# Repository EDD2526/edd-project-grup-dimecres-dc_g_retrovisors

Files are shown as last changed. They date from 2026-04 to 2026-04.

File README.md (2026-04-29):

View this project on [CADLAB.io](https://cadlab.io/project/30190). 

# Projecte Retrovisors

>**Autors:Carlos Soler Fernandez, Ingrid López Sánchez ** 
>**Versió: final (v.3)**

----------

## Objectiu

>Poder obrir y tancar els retrovisors del cotxe
>Crear els leds de canvi de dirección i angle mort 
>Crear un defoger
>Poder ajustar els retrovisors del cotxe
>Dissenyar i fabricar un sistema electrònic integral per al control de retrovisors
>Gestionar els tres motors amb els finals de carrera on calgui
>Incorporar un sistema que medeixi quan es produeix enlluernament
>Planificar el muntatge de la placa tenint en compte les regles i esoecificacions del fabricant 
>Incorporar un sistema de calefacció i sensors digitals d'angle mort
>Assegurant la viabilitat tècnica i econòmica des del prototip fins a la producció a gran escala

## Diagrama de blocs

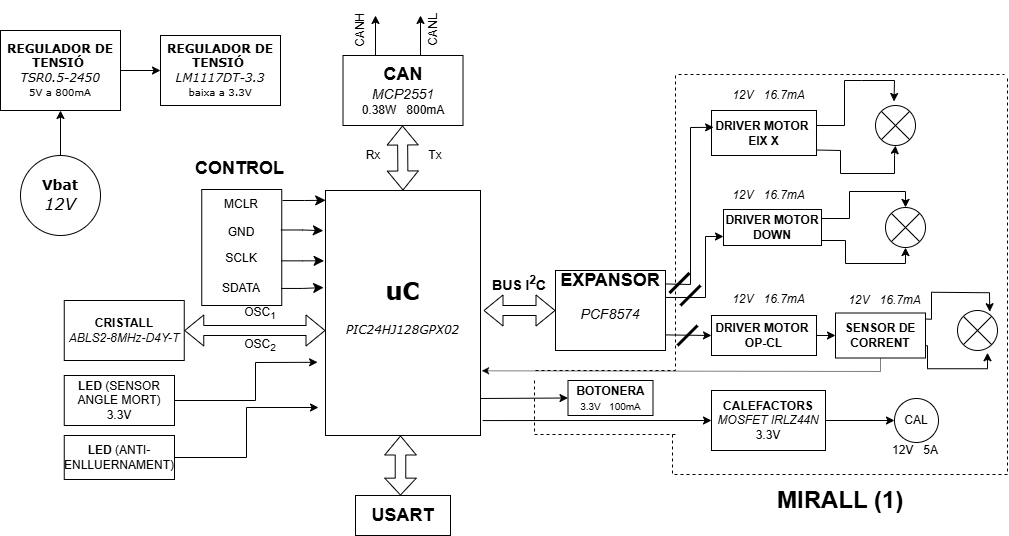
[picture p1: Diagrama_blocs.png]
Diagrama de Blocs


### Descripció/funcionalitat de cada bloc

  *

-----------

## Requisits / Especificacions

  * Alimentació; 12V, regulada 5V
  * Microcontrolador PIC18xxxxxxxxx
  * ...

-----------

## Components

| Descripci&#243; | Ref | Package |Datasheet | Prove&#239;dor | Preu | Unitats |
| --- | --- | --- | --- | ---| --- | --- |
| Microcontrolador | PIC18F26Q83-I/SS | SOIC-28 |[Datasheet](https://www.mouser.es/datasheet/2/268/PIC18F27_47_57Q83_Preliminary_Data_Sheet_40002265B-2887591.pdf) | [Mouser](https://www.mouser.es/c/?q=PIC18F27Q83-I%2FSO)| 2,17&euro;| 1x |
| XTAL-Ressonador | CSTCR7M99G53-R0 | SMD |[Datasheet](https://www.mouser.es/datasheet/2/281/p16e-522700.pdf) | [Mouser](https://www.mouser.es/ProductDetail/Murata-Electronics/CSTCR7M99G53-R0?qs=Zd9RUO93%2Fo7cnwzsujIkpA%3D%3D)  | 0,27&euro; | 1x |

-----------

## Software

### Eines:

  * KiCad 9.0 o superior
  * 

### Configuraci&#243; :

  * 

### Funcionalitats:

  * 

-----------

## Historial de canvis

| Data | Autor | Branch | Versi&#243; | Descripci&#243; |
| --- | --- | --- | --- | --- |
| 11/03/2026 | iingridlopez | Master | prova | Inici del projecte 
| 17/03/2026 | canals-ub | Master | Backlink added | Backlink to CADLAB.io has been added. 
| 17/03/2026 | Carlosolerfernandez | Master | Create project kicad | Inici del projecte en KiCad 
| 17/03/2026 | Carlosolerfernandez | Master | Inici kiCat | Primera versió de l'esquemàtic 
| 17/03/2026 | Carlosolerfernandez | Master | Inici proyecta kicat | Configuració de fitxers inicials 
| 17/03/2026 | Carlosolerfernandez | Master | Etapa de alimentació 1 | Disseny de la primera part d'alimentació 
| 17/03/2026 | Carlosolerfernandez | Master | Etapa de alimentacio completa | Finalització de l'etapa d'alimentació 
| 17/03/2026 | Carlosolerfernandez | Master | Alimentacio finalitzada e inici de micro | Transició al disseny del microcontrolador 
| 18/03/2026 | Carlosolerfernandez | Master | microcontrolador i driver | Afegit microcontrolador i perifèrics 
| 22/03/2026 | Carlosolerfernandez | Master | Correcio gnd, proposicio canvi de micro | Correcció de masses i revisió de components 
| 23/03/2026 | Carlosolerfernandez | Master | Reorganització proyecte, inici conexions CAN | Gestió del bus CAN 
| 23/03/2026 | Carlosolerfernandez | Master | Part Micro quasi completat | Falta afegir etiquetes de potencia 
| 24/03/2026 | Carlosolerfernandez | Master | Microprocessador finalissim | Placement de alimentacion y micro 
| 25/03/2026 | Carlosolerfernandez | Master | Diagrama de Blocs Afegit | Canvi del swicht1 to push botton5 
| 29/03/2026 | iingridlopez | Branca Nova | Creacio de branca nova i update | Inici de nova branca de treball 
| 07/04/2026 | iingridlopez | Master | actualització (NO VERSIÓ FINAL) | Sincronització de canvis |
| 08/04/2026 | iingridlopez | Master | esquematic + placement | Falta routing dels drivers 
| 08/04/2026 | Carlosolerfernandez | Master | README | Creació del fitxer de documentació 
| 08/04/2026 | iingridlopez | Master | añadido el readme | Actualització de documentació 
| 08/04/2026 | Carlosolerfernandez | Master | Modificació placement | Ajustos en la placa 
| 08/04/2026 | iingridlopez | Master | prueba para unir a la main | Test de merge 
| 08/04/2026 | iingridlopez | Master | Merge con resolución de conflictos | Unió de branques en KiCad 
| 08/04/2026 | Carlosolerfernandez | Master | afegim diagrama | Actualització gràfica del projecte 
| 08/04/2026 | Carlosolerfernandez | Master | Correccion Readme | Revisió de textos 
| 08/04/2026 | Carlosolerfernandez | Master | eliminamos GND PWR | Modificació de tots els GND 
| 10/04/2026 | iingridlopez | Master | millora de placement | Optimització d'espai 
| 13/04/2026 | Carlosolerfernandez | Master | Enrotament Part digital finalitzada | Finalització del routing digital |

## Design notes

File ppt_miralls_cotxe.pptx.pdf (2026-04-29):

# MÒDUL D’AUTOMÒBIL: RETROVISORS

# Posar en pràctica els coneixements adquirits durant el curs per a desenvolupar un sistema electrònic seguint el flux de disseny de PCBs amb temàtica de projectes

d’automoció.

## Grau d’Enginyeria Electrònica de Telecomunicacions: Facultat de Física- UB

## Eines de Disseny - 2026

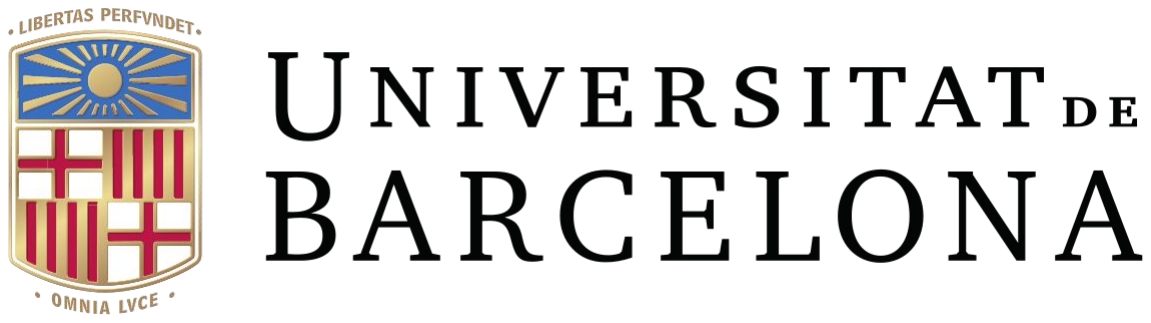
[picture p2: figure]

## Carlos Soler Fernandez, Ingrid Lopez Sanchez

Objectius | Components | Diagrama de blocs | Esquemàtic | Simulació | Layout | Pressupost

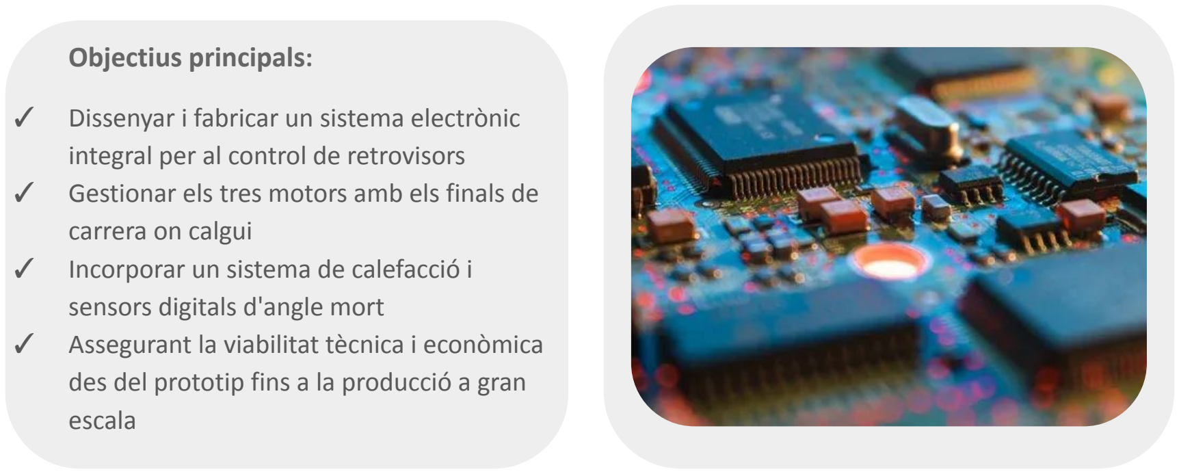
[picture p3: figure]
Objectius principals:; integral per al control de retrovisors; carrera on calgui ✓ Incorporar un sistema de calefacció i; sensors digitals d'angle mort; escala

## ✓ Dissenyar i fabricar un sistema electrònic

## ✓ Gestionar els tres motors amb els finals de

## ✓ Assegurant la viabilitat tècnica i econòmica des del prototip fins a la producció a gran

1

## DATASHEETS

## PIC24HJ128GPX02 (https://ww1.microchip.com/downloads/en/DeviceDoc/70293G.pdf)

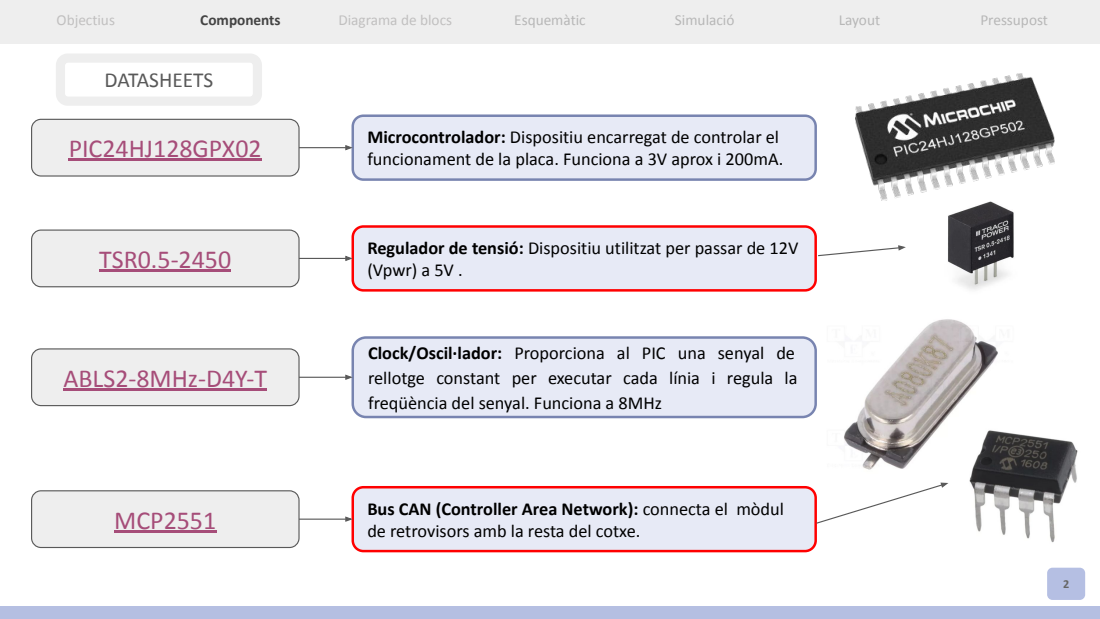
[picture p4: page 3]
TSR0.5-2450; ABLS2-8MHz-D4Y-T; MCP2551

Microcontrolador: Dispositiu encarregat de controlar el
funcionament de la placa. Funciona a 3V aprox i 200mA.

Regulador de tensió: Dispositiu utilitzat per passar de 12V
(Vpwr) a 5V .

Clock/Oscil·lador: Proporciona al PIC una senyal de
rellotge constant per executar cada línia i regula la
freqüència del senyal. Funciona a 8MHz

Bus CAN (Controller Area Network): connecta el mòdul
de retrovisors amb la resta del cotxe.

## DATASHEETS

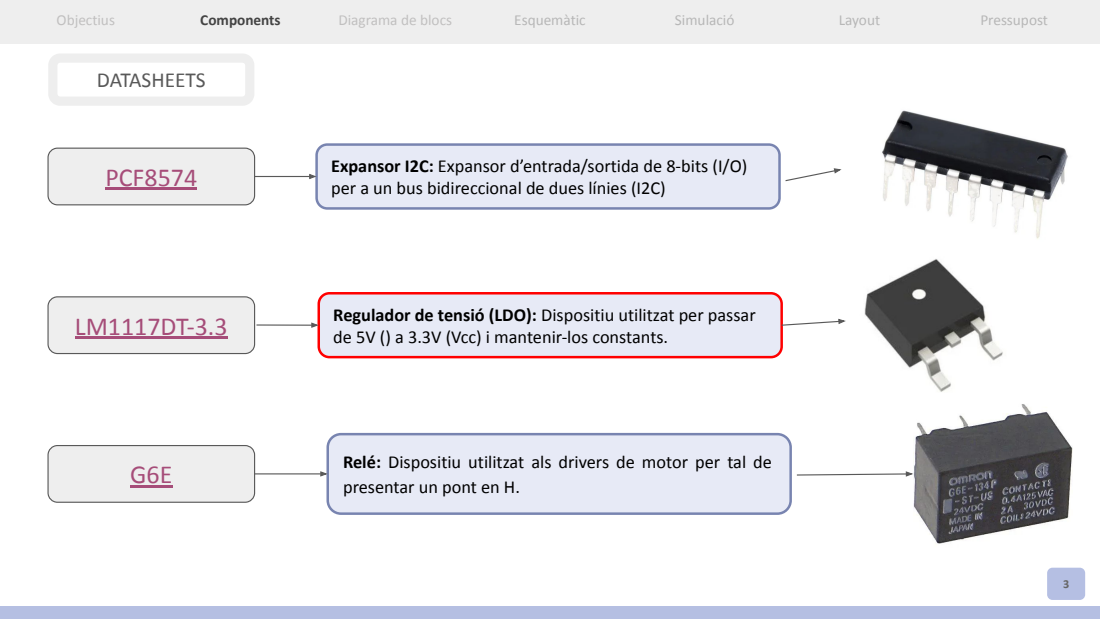
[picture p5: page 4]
PCF8574

Expansor I2C: Expansor d’entrada/sortida de 8-bits (I/O)
per a un bus bidireccional de dues línies (I2C)

Regulador de tensió (LDO): Dispositiu utilitzat per passar
de 5V () a 3.3V (Vcc) i mantenir-los constants.

Relé: Dispositiu utilitzat als drivers de motor per tal de
presentar un pont en H.

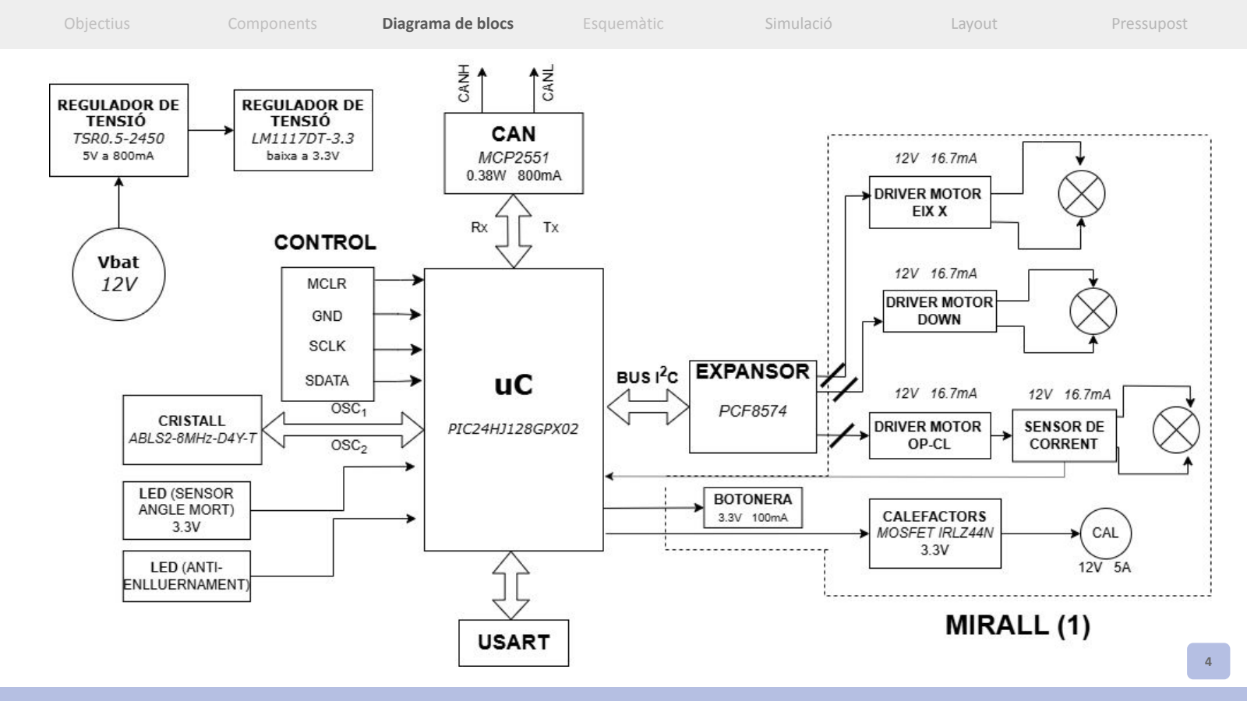
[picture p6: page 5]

4

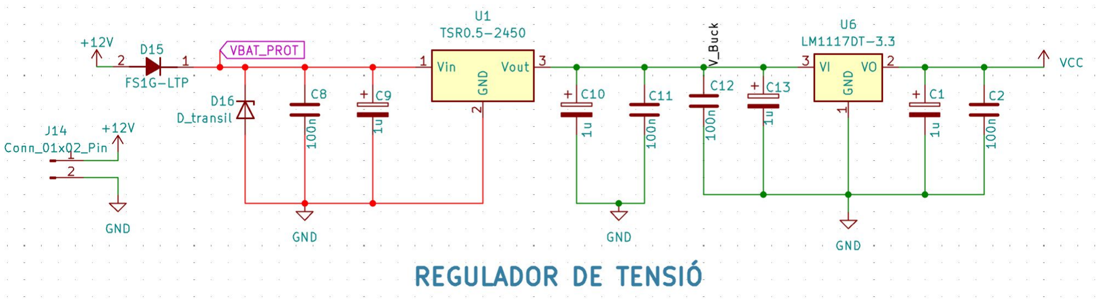
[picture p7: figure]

5

## REGULADOR DE TENSIÓ

## LED’S

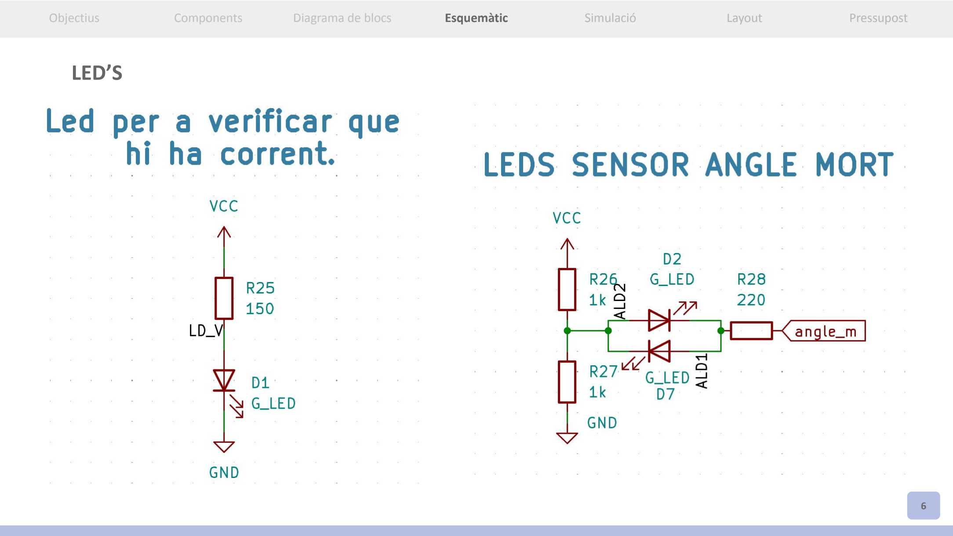
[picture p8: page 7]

6

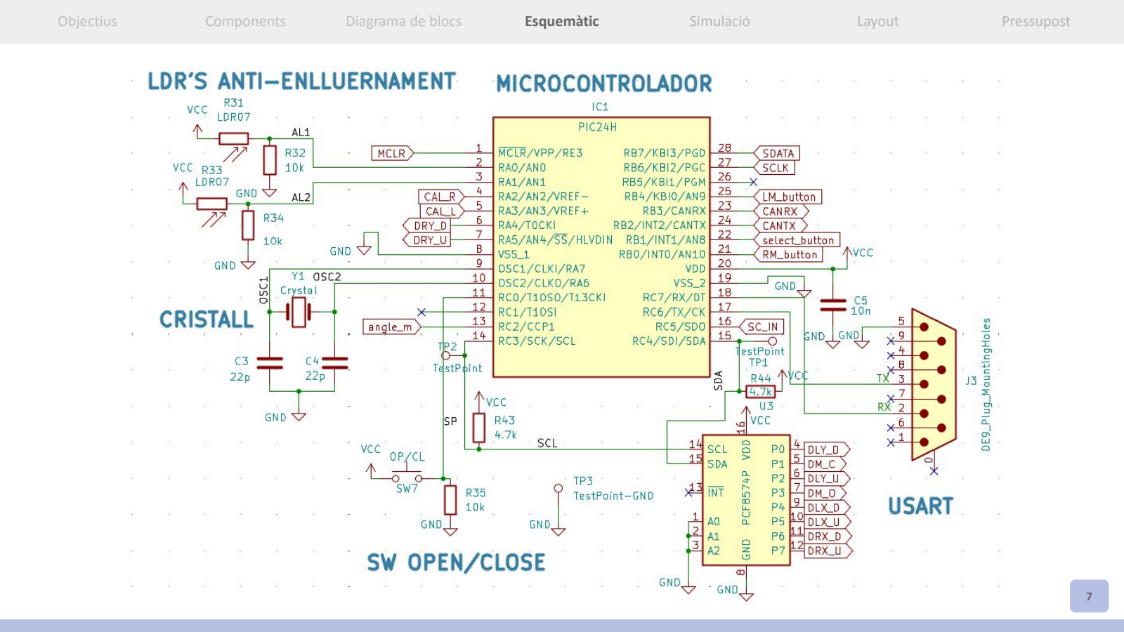
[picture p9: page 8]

7

8

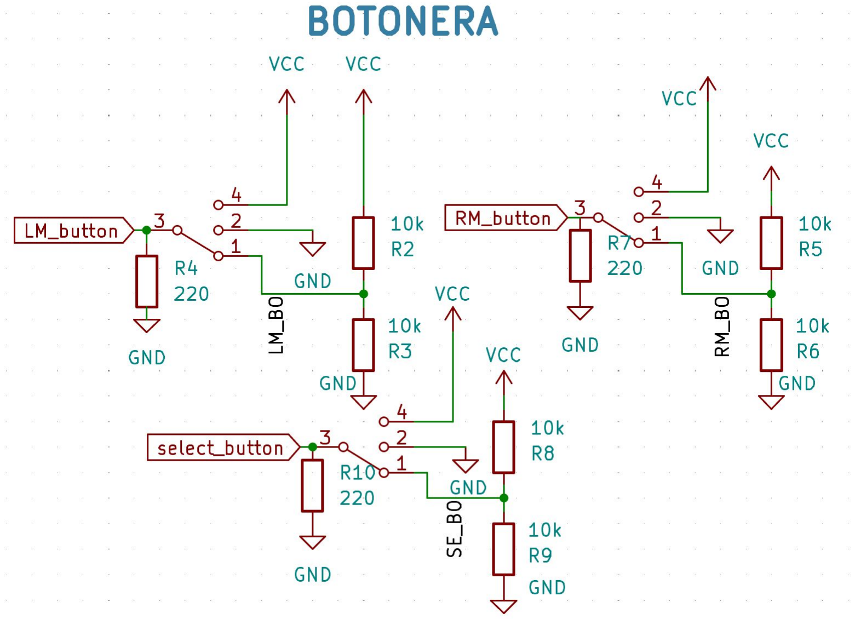
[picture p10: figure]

## FASE DIGITAL

## FASE DIGITAL

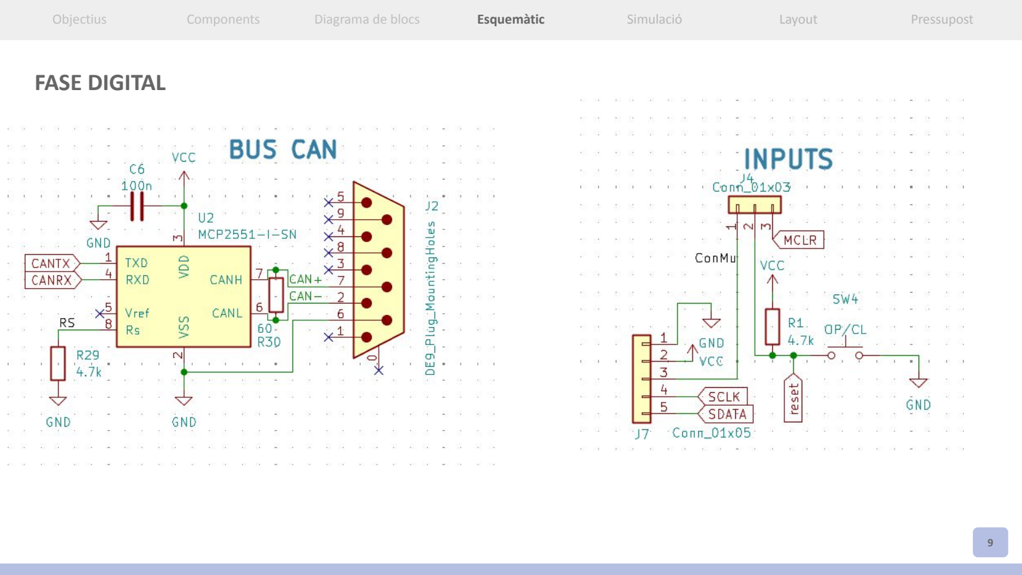
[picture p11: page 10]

9

## FASE DE POTÈNCIA

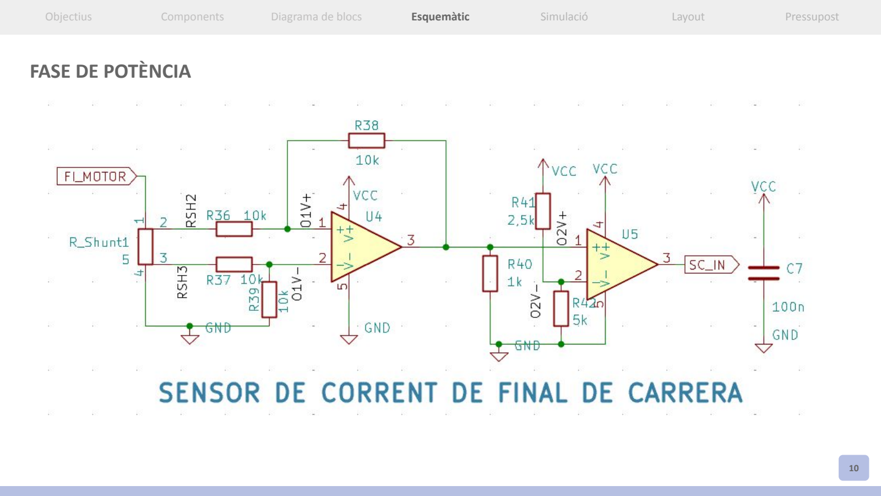
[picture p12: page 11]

10

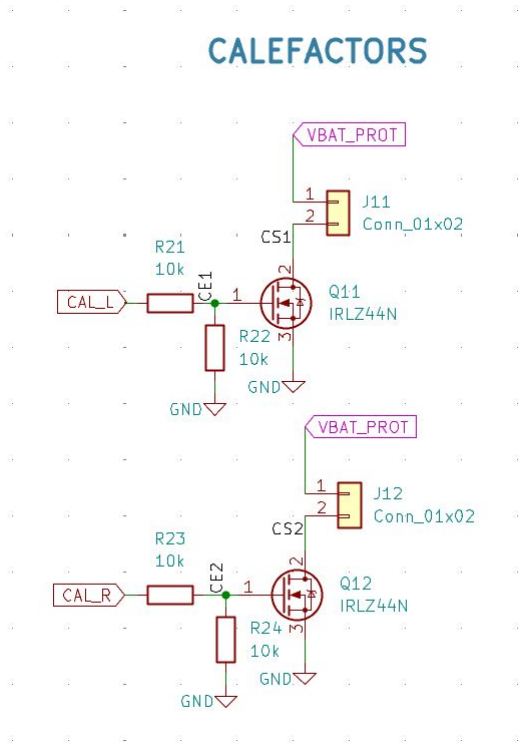
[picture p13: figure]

11

## FASE DE POTÈNCIA

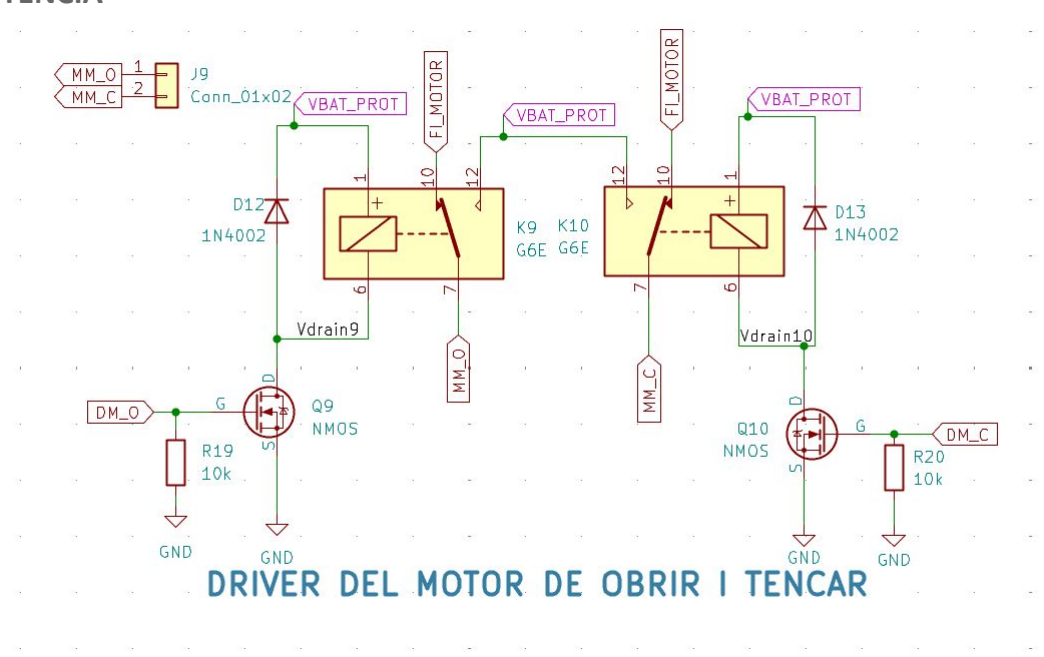
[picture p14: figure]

12

## FASE DE POTÈNCIA

## FASE DE POTÈNCIA

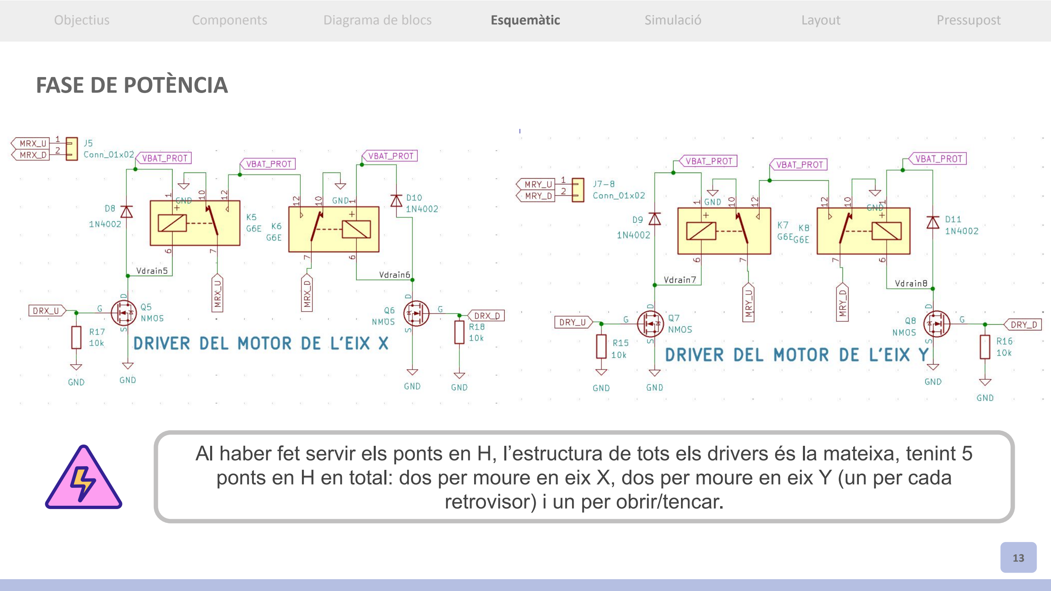
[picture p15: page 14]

13

Al haber fet servir els ponts en H, l’estructura de tots els drivers és la mateixa, tenint 5

## ponts en H en total: dos per moure en eix X, dos per moure en eix Y (un per cada

retrovisor) i un per obrir/tencar.

SIMULACIÓ: SENSOR DE CORRENT;

## FINAL DE CARRERA OP/CL

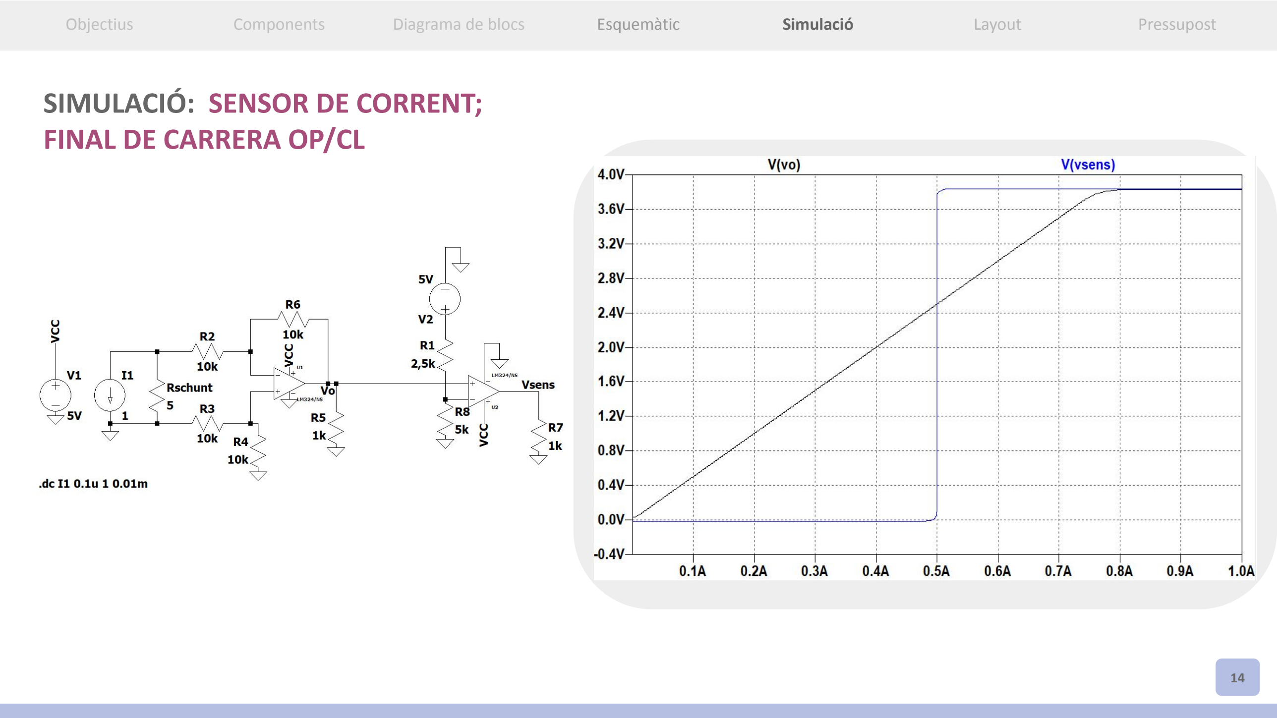
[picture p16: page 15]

14

## SIMULACIÓ: RELÉS

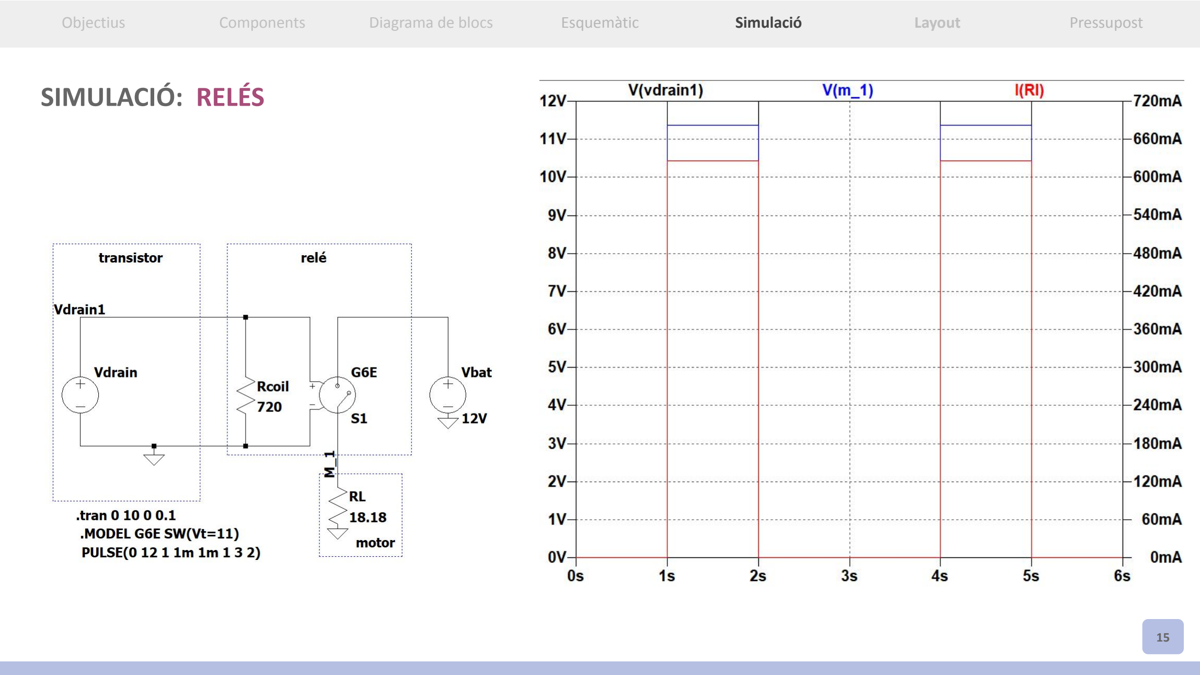
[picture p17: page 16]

15

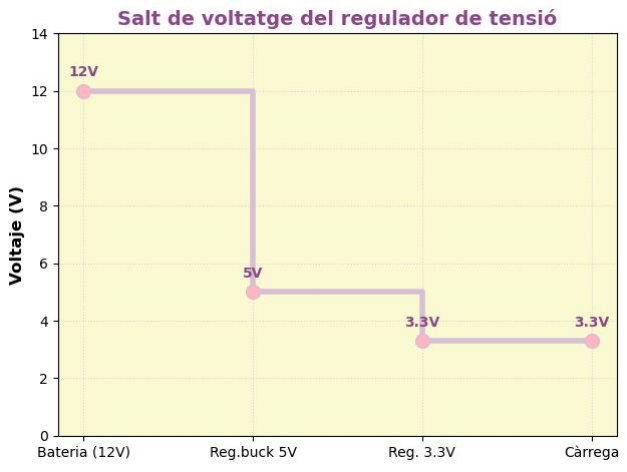
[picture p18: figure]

16

## SIMULACIÓ: PART ALIMENTACIÓ, BUCK I REGULADOR DE TENSIÓ

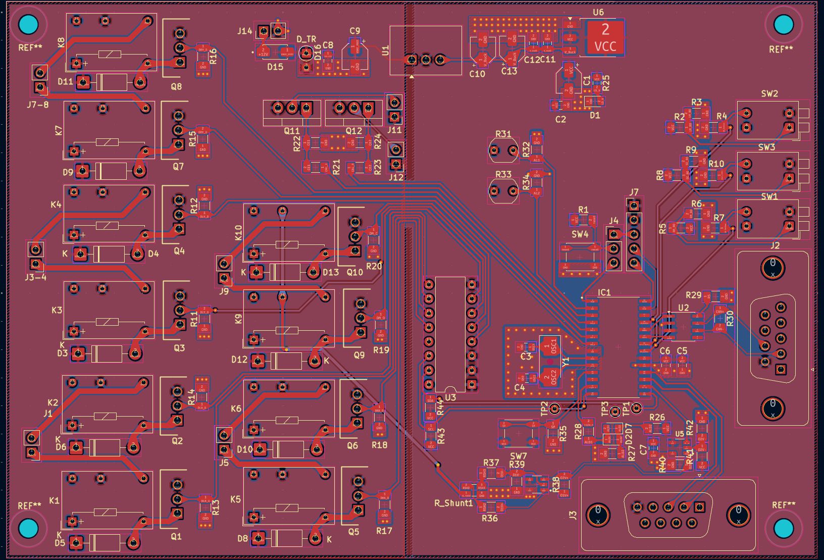
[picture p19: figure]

17

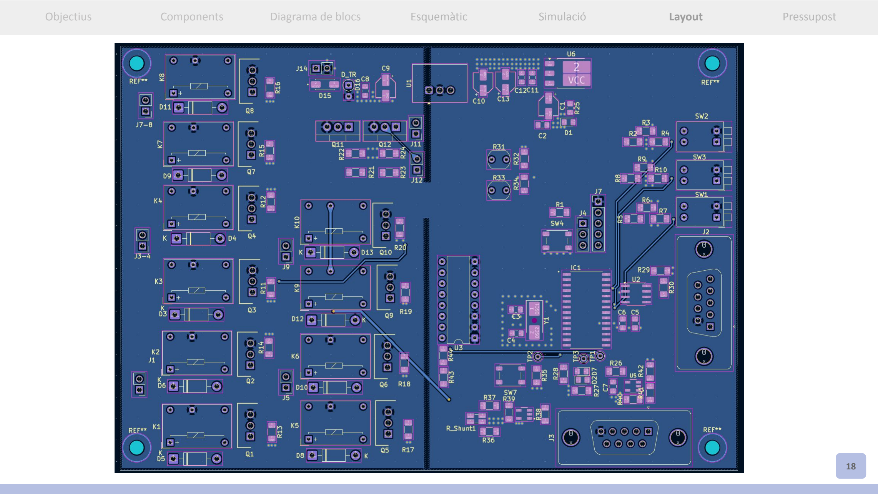
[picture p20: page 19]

18

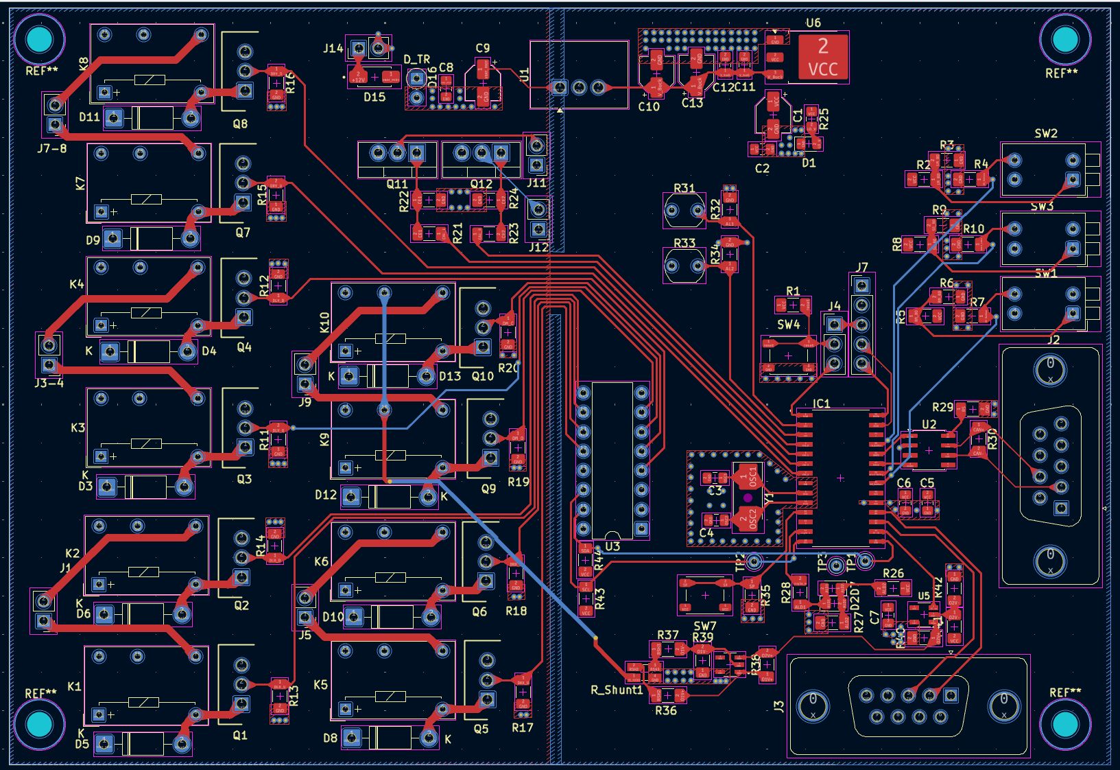
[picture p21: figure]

19

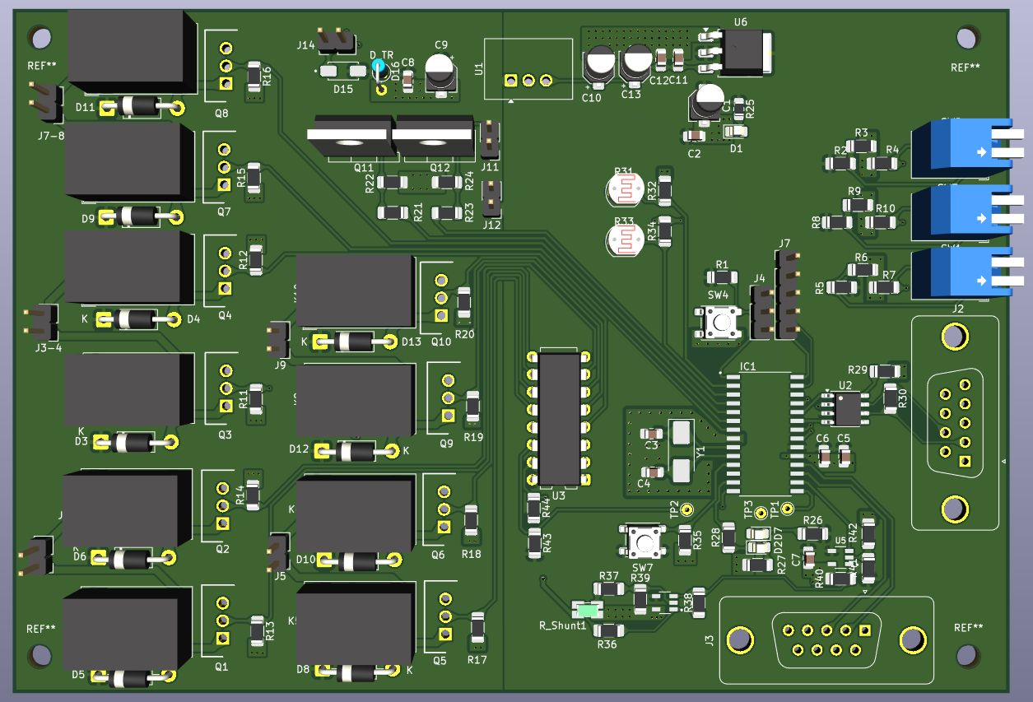
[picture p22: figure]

20

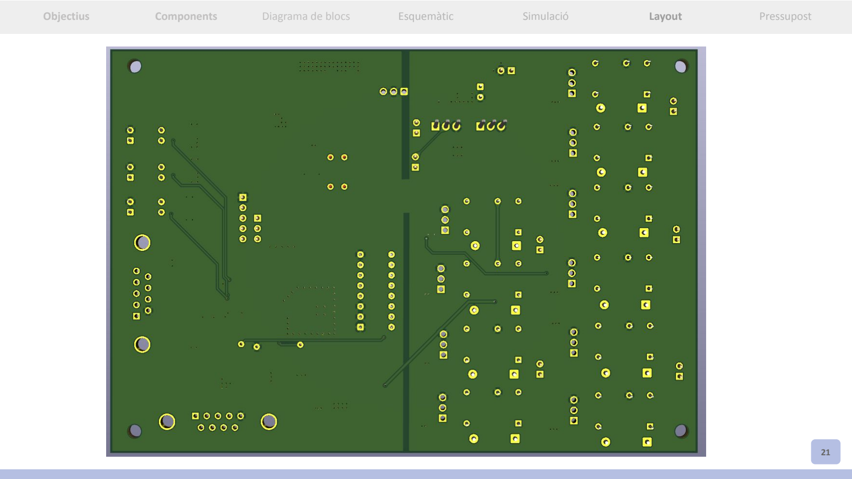
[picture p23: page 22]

21

22

| x1 PLACA | x10 PLAQUES | x50 PLAQUES | x1000 PLAQUES | x20000 PLAQUES
PREU TOTAL COMPONENTS (€) | 67,47 | 625,04 | 2876,27 | 42681,19 | 842069,8

23

| x1 PLACA | x10 PLAQUES | x50 PLAQUES | x1000 PLAQUES | x20000 PLAQUES
PREU TOTAL COMPONENTS (€) | 67,47 | 625,04 | 2876,27 | 42681,19 | 842069,8
PREU ELABORACIÓ PLACA (€) | 11,50 | 14,50 | 37 | 390,41 | 7028,52
PREU PER PLACA (€) | 78,97 | 63,95 | 58,27 | 44,07 | 42,45
PREU TOTAL (€) | 78,97 | 639,54 | 2913,27 | 44071,6 | 849098,32

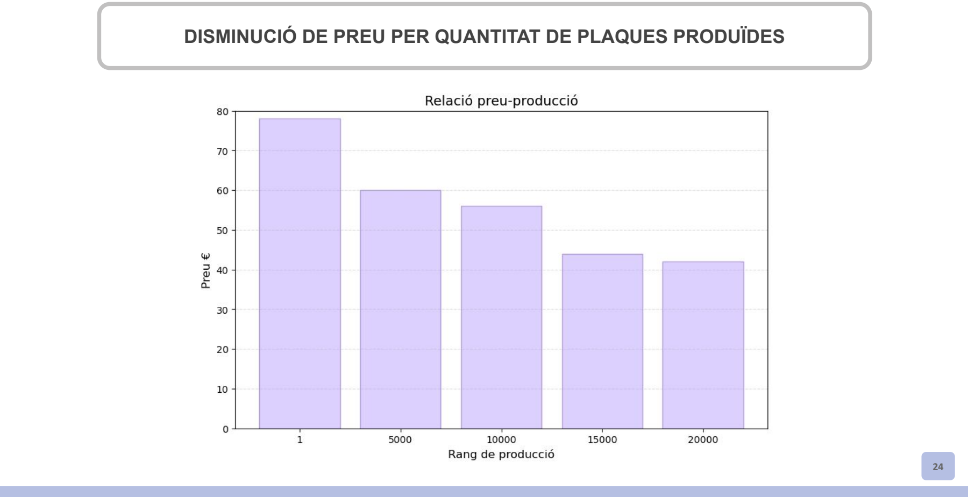
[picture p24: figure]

## DISMINUCIÓ DE PREU PER QUANTITAT DE PLAQUES PRODUÏDES

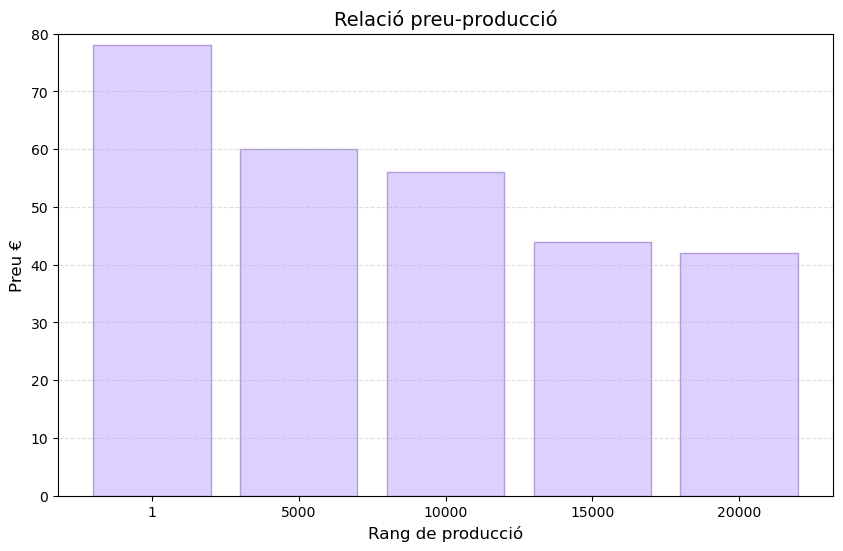
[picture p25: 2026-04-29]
graf_preu_prod.png

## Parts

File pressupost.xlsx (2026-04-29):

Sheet: Retrovisors_Carlos_Soler_Ingrid
# | Reference | Qty | Value | Footprint | DNP | P x1 (€) | P x10 (€) | P x50 (€) | P x1000 (€) | P x20000 (€)
1 | C1, C9, C10, C13 | 4 | 1u | Capacitor_SMD:CP_Elec_4x5.7
2 | C2, C6, C7, C8, C11, C12 | 6 | 100n | Capacitor_SMD:C_0805_2012Metric_Pad1.18x1.45mm_HandSolder
3 | C3, C4 | 2 | 22p | Capacitor_SMD:C_0805_2012Metric_Pad1.18x1.45mm_HandSolder
4 | C5 | 1 | 10n | Capacitor_SMD:C_0805_2012Metric_Pad1.18x1.45mm_HandSolder
5 | D1, D2, D7 | 3 | G_LED | LED_SMD:LED_0805_2012Metric_Pad1.15x1.40mm_HandSolder |  | 0.38 | 2.46 | 12.3 | 94.73 | 1994.6
6 | D3, D4, D5, D6, D8, D9, D10, D11, D12, D13 | 10 | 1N4002 | Diode_THT:D_DO-41_SOD81_P10.16mm_Horizontal
7 | D15 | 1 | FS1G-LTP | AA_footprints:DIOM5225X244N
8 | D16 | 1 | D_transil | Diode_THT:D_DO-35_SOD27_P2.54mm_Vertical_AnodeUp
9 | IC1 | 1 | PIC24H | AA_footprints:SOIC127P1030X265-28N
10 | J1, J3-4, J5, J7-8, J9, J11, J12 | 7 | Conn_01x02 | Connector_PinHeader_2.54mm:PinHeader_1x02_P2.54mm_Vertical
11 | J2, J3 | 2 | DE9_Plug_MountingHoles | AA_footprints:DSUB-9_Female_Vertical_Pitch2.77x2.84mm_MountingHoles
12 | J4 | 1 | Conn_01x03 | Connector_PinHeader_2.54mm:PinHeader_1x03_P2.54mm_Vertical
13 | J7 | 1 | Conn_01x05 | Connector_PinHeader_2.54mm:PinHeader_1x05_P2.54mm_Vertical
14 | J14 | 1 | Conn_01x02_Pin | Connector_PinHeader_2.54mm:PinHeader_1x02_P2.54mm_Vertical
15 | K1, K2, K3, K4, K5, K6, K7, K8, K9, K10 | 10 | G6E | Relay_THT:Relay_SPDT_Omron_G6E
16 | Q1, Q2, Q3, Q4, Q5, Q6, Q7, Q8, Q9, Q10 | 10 | NMOS | AA_footprints:TO254P470X1016X1965-3P
17 | Q11, Q12 | 2 | IRLZ44N | Package_TO_SOT_THT:TO-220-3_Vertical
18 | R1, R29, R43, R44 | 4 | 4.7k | Resistor_SMD:R_1206_3216Metric_Pad1.30x1.75mm_HandSolder
19 | R2, R3, R5, R6, R8, R9, R11, R12, R13, R14, R15, R16, R17, R18, R19, R20, R21, R22, R23, R24, R32, R34, R35, R36, R37, R38, R39 | 27 | 10k | Resistor_SMD:R_1206_3216Metric_Pad1.30x1.75mm_HandSolder
20 | R4, R7, R10, R28 | 4 | 220 | Resistor_SMD:R_1206_3216Metric_Pad1.30x1.75mm_HandSolder
21 | R25 | 1 | 150 | Resistor_SMD:R_0805_2012Metric_Pad1.20x1.40mm_HandSolder
22 | R26, R27, R40 | 3 | 1k | Resistor_SMD:R_1206_3216Metric_Pad1.30x1.75mm_HandSolder
23 | R30 | 1 | 60 | Resistor_SMD:R_1206_3216Metric_Pad1.30x1.75mm_HandSolder
24 | R31, R33 | 2 | LDR07 | OptoDevice:R_LDR_5.1x4.3mm_P3.4mm_Vertical
25 | R41 | 1 | 2,5k | Resistor_SMD:R_1206_3216Metric_Pad1.30x1.75mm_HandSolder
26 | R42 | 1 | 5k | Resistor_SMD:R_1206_3216Metric_Pad1.30x1.75mm_HandSolder
27 | R_Shunt1 | 1 | 5 | Resistor_SMD:R_Shunt_Ohmite_LVK12
28 | SW1, SW2, SW3 | 3 | SW_DP3T | Button_Switch_THT:SW_DIP_SPSTx02_Piano_10.8x6.64mm_W7.62mm_P2.54mm
29 | SW4, SW7 | 2 | OP/CL | Button_Switch_SMD:SW_SPST_PTS647_Sx38
30 | TP1, TP2 | 2 | TestPoint | TestPoint:TestPoint_THTPad_D1.5mm_Drill0.7mm
31 | TP3 | 1 | TestPoint-GND | TestPoint:TestPoint_THTPad_D1.5mm_Drill0.7mm
32 | U1 | 1 | TSR0.5-2450 | Converter_DCDC:Converter_DCDC_TRACO_TSR0.5-24xx_TSR0.5-24xxx_THT
33 | U2 | 1 | MCP2551-I-SN | Package_SO:SOIC-8_3.9x4.9mm_P1.27mm
34 | U3 | 1 | PCF8574P | Package_DIP:DIP-16_W7.62mm
35 | U4, U5 | 2 | type="X" model="OPAMP" lib="" | AA_footprints:SOT95P280X145-5N
36 | U6 | 1 | LM1117DT-3.3 | Package_TO_SOT_SMD:TO-252-3_TabPin2
37 | Y1 | 1 | Crystal | Crystal:Crystal_SMD_Abracon_ABM3-2Pin_5.0x3.2mm_HandSoldering

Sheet: total_components
Concepto | x1 PLACA | x10 PLAQUES | x50 PLAQUES | x1000 PLAQUES | x20000 PLAQUES
PREU TOTAL COMPONENTS (€) | 67.47 | 625.04 | 2876.27 | 42681.19 | 842069.8

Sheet: total_placa
Concepto | x1 PLACA | x10 PLAQUES | x50 PLAQUES | x1000 PLAQUES | x20000 PLAQUES
PREU TOTAL COMPONENTS (€) | 67.47 | 625.04 | 2876.27 | 42681.19 | 842069.8 | TOTAL | 1 | 10 | 50 | 1000 | 20000
PREU ELABORACIÓ PLACA (€) | 11.5 | 14.5 | 37 | 390.41 | 7028.52 | PREU TOTAL (€) | 78.97 | 639.54 | 2913.27 | 44071.6 | 849098.32
PREU PER PLACA (€) | 78.97 | 63.95 | 58.27 | 44.07 | 42.45
PREU TOTAL (€) | 78.97 | 639.54 | 2913.27 | 44071.6 | 849098.32

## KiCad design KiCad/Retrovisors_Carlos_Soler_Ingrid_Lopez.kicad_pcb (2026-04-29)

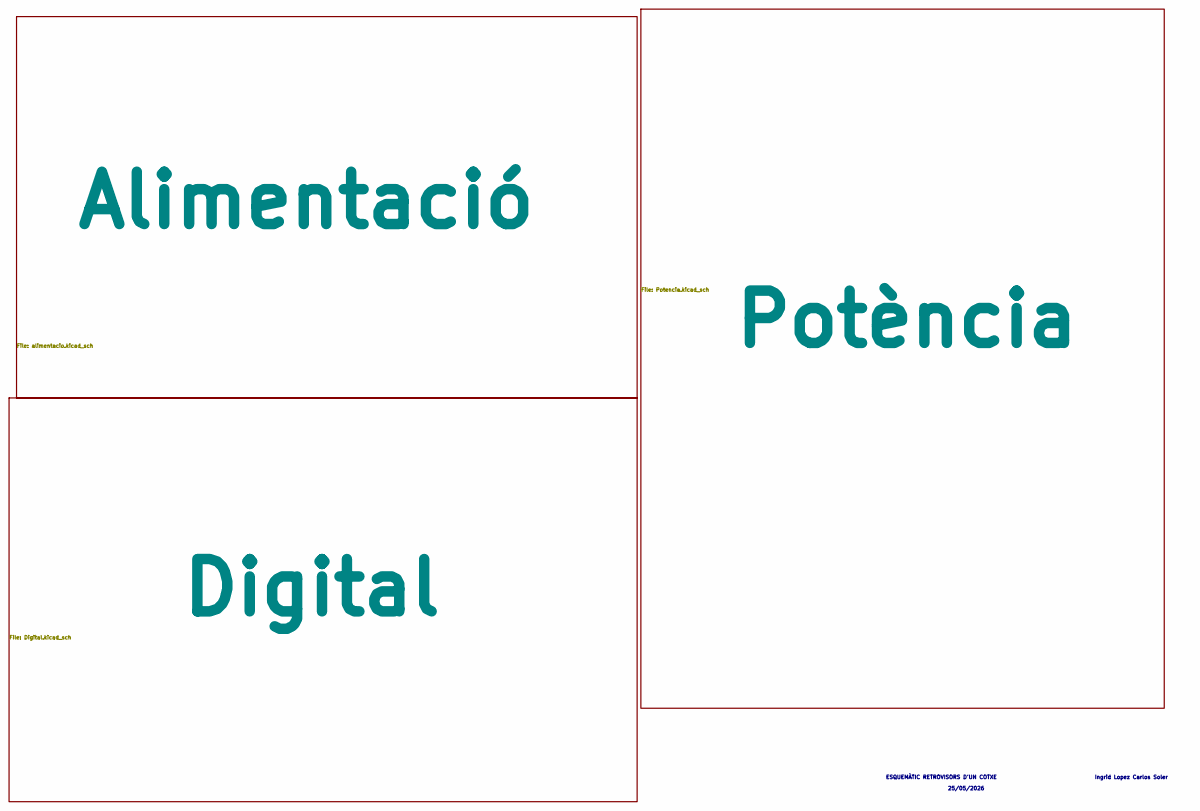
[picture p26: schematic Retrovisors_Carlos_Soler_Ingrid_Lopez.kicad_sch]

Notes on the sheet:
Ingrid Lopez Carlos Soler
ESQUEMÀTIC RETROVISORS D'UN COTXE
25/05/2026

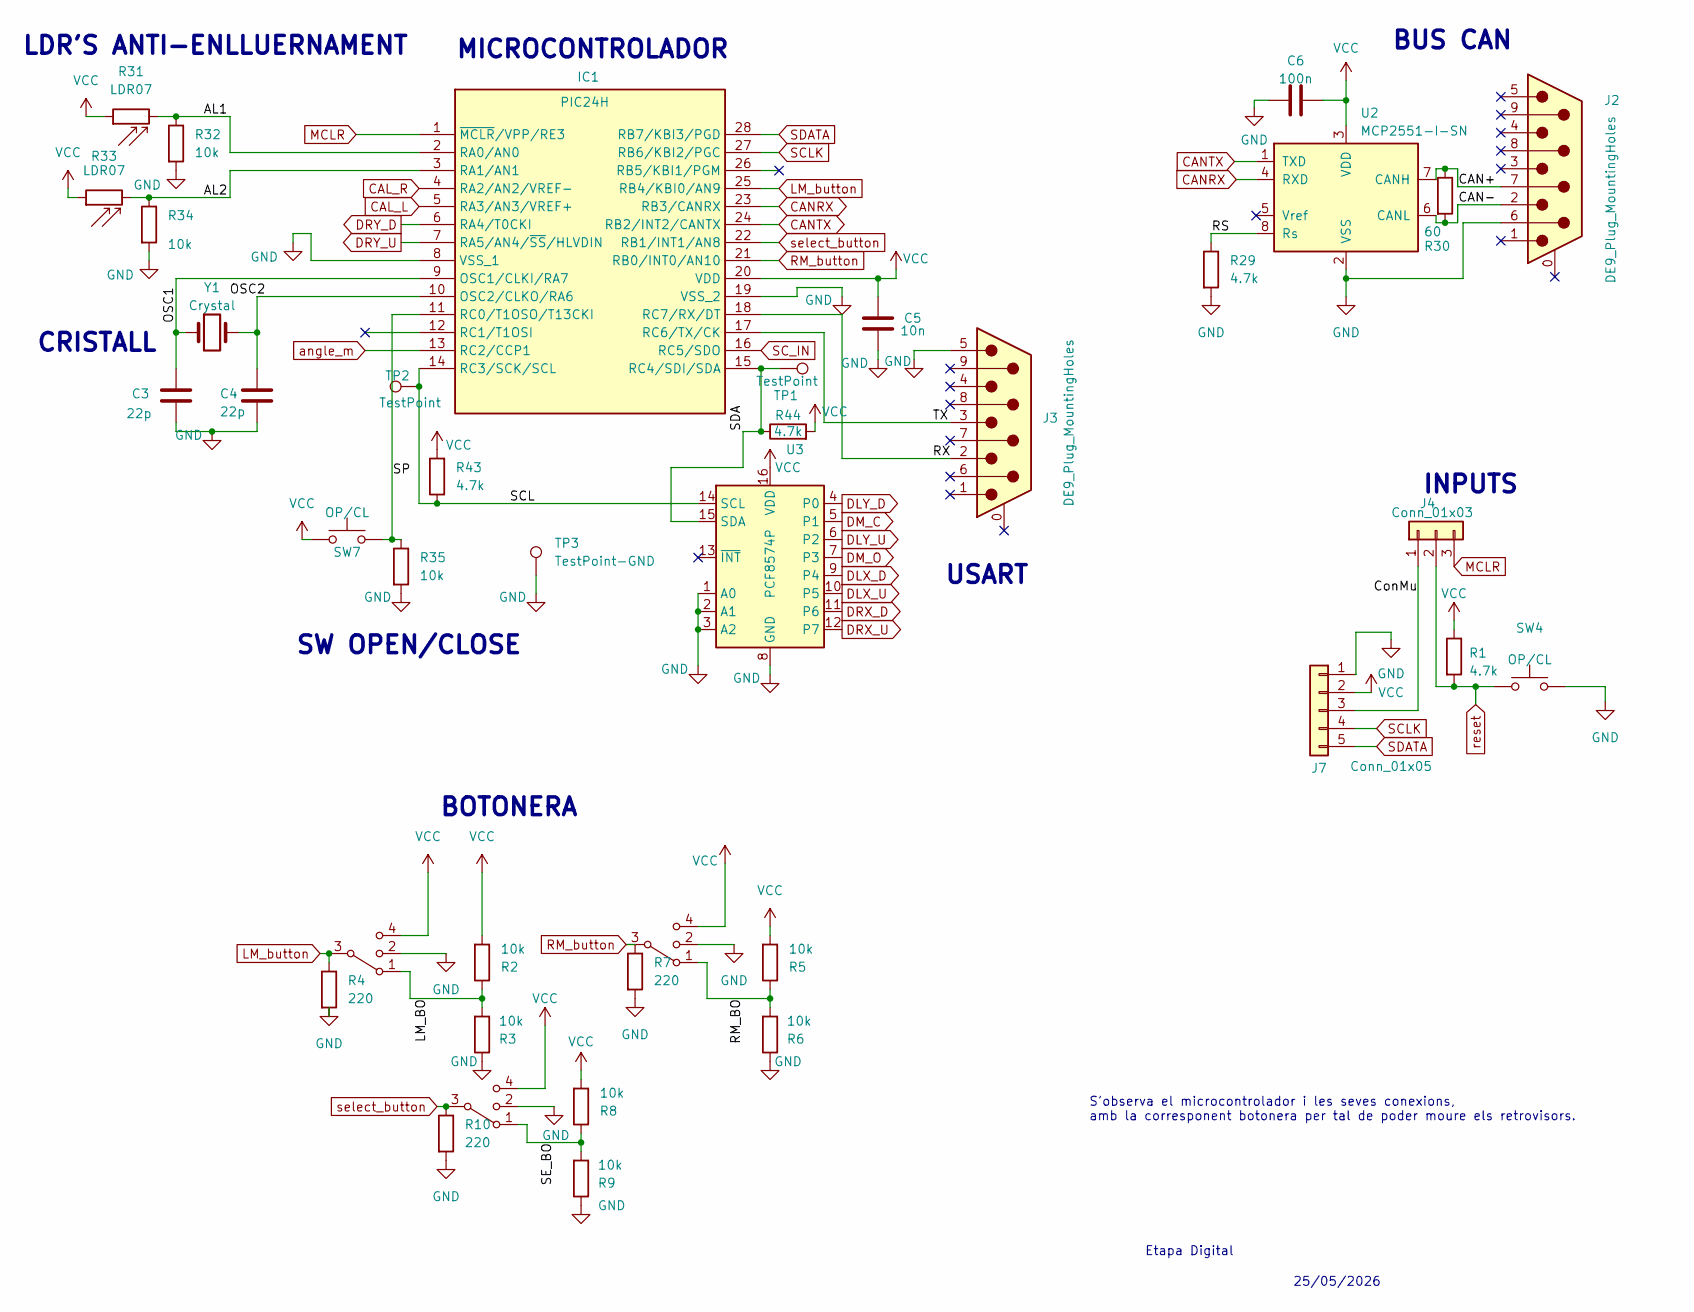
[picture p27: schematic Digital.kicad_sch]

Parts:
C3, C4: 22p; C_0805_2012Metric_Pad1.18x1.45mm_HandSolder
C5: 10n; C_0805_2012Metric_Pad1.18x1.45mm_HandSolder
C6: 100n; C_0805_2012Metric_Pad1.18x1.45mm_HandSolder
IC1: PIC24H; SOIC127P1030X265-28N; Manufacturer_Part_Number PIC18F2580-I/SO; Mouser Part Number 579-PIC18F2580-I/SO
J2, J3: DE9_Plug_MountingHoles; DSUB-9_Female_Vertical_Pitch2.77x2.84mm_MountingHoles
J4: Conn_01x03; PinHeader_1x03_P2.54mm_Vertical
J7: Conn_01x05; PinHeader_1x05_P2.54mm_Vertical
R1, R29, R43, R44: 4.7k; R_1206_3216Metric_Pad1.30x1.75mm_HandSolder
R2, R3, R5, R6, R8, R9, R32, R34, R35: 10k; R_1206_3216Metric_Pad1.30x1.75mm_HandSolder
R4, R7, R10: 220; R_1206_3216Metric_Pad1.30x1.75mm_HandSolder
R30: 60; R_1206_3216Metric_Pad1.30x1.75mm_HandSolder
R31, R33: LDR07; R_LDR_5.1x4.3mm_P3.4mm_Vertical
SW1, SW2, SW3: SW_DP3T; SW_DIP_SPSTx02_Piano_10.8x6.64mm_W7.62mm_P2.54mm
SW4, SW7: OP/CL; SW_SPST_PTS647_Sx38
TP1, TP2: TestPoint; TestPoint_THTPad_D1.5mm_Drill0.7mm
TP3: TestPoint-GND; TestPoint_THTPad_D1.5mm_Drill0.7mm
U2: MCP2551-I-SN; SOIC-8_3.9x4.9mm_P1.27mm
U3: PCF8574P; DIP-16_W7.62mm
Y1: Crystal; Crystal_SMD_Abracon_ABM3-2Pin_5.0x3.2mm_HandSoldering

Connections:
/Digital/AL1: IC1.2 (RA0/AN0), R31.2, R32.1
/Digital/AL2: IC1.3 (RA1/AN1), R33.2, R34.1
/Digital/CAN+: J2.7, R30.1, U2.7 (CANH)
/Digital/CAN-: J2.2, R30.2, U2.6 (CANL)
/Digital/ConMu: J4.1, J7.3
/Digital/LM_BO: R2.1, R3.2, SW2.1
/Digital/OSC1: C3.1, IC1.9 (OSC1/CLKI/RA7), Y1.1
/Digital/OSC2: C4.1, IC1.10 (OSC2/CLKO/RA6), Y1.2
/Digital/RM_BO: R5.1, R6.2, SW1.1
/Digital/RS: R29.1, U2.8 (Rs)
/Digital/RX: IC1.18 (RC7/RX/DT), J3.2
/Digital/SCL: IC1.14 (RC3/SCK/SCL), R43.1, TP2.1, U3.14 (SCL)
/Digital/SDA: IC1.15 (RC4/SDI/SDA), R44.1, TP1.1, U3.15 (SDA)
/Digital/SE_BO: R8.1, R9.2, SW3.1
/Digital/SP: IC1.11 (RC0/T1OSO/T13CKI), R35.1, SW7.2
/Digital/TX: IC1.17 (RC6/TX/CK), J3.3
CAL_L: IC1.5 (RA3/AN3/VREF+); also elsewhere on the board
CAL_R: IC1.4 (RA2/AN2/VREF-); also elsewhere on the board
CANRX: IC1.23 (RB3/CANRX), U2.4 (RXD)
CANTX: IC1.24 (RB2/INT2/CANTX), U2.1 (TXD)
DLX_D: U3.9 (P4); also elsewhere on the board
DLX_U: U3.10 (P5); also elsewhere on the board
DLY_D: U3.4 (P0); also elsewhere on the board
DLY_U: U3.6 (P2); also elsewhere on the board
DM_C: U3.5 (P1); also elsewhere on the board
DM_O: U3.7 (P3); also elsewhere on the board
DRX_D: U3.11 (P6); also elsewhere on the board
DRX_U: U3.12 (P7); also elsewhere on the board
DRY_D: IC1.6 (RA4/T0CKI); also elsewhere on the board
DRY_U: IC1.7 (RA5/AN4/~SS/HLVDIN); also elsewhere on the board
GND: C3.2, C4.2, C5.2, C6.1, IC1.8 (VSS_1), IC1.19 (VSS_2), J2.6, J3.5, J7.1, R3.1, R4.2, R6.1, R7.2, R9.1, R10.2, R29.2, R32.2, R34.2, R35.2, SW1.2, SW2.2, SW3.2, SW4.2, TP3.1, U2.2 (VSS), U3.1 (A0), U3.2 (A1), U3.3 (A2), U3.8 (GND); also elsewhere on the board
LM_button: IC1.25 (RB4/KBI0/AN9), R4.1, SW2.3
MCLR: IC1.1 (~MCLR/VPP/RE3), J4.3
RM_button: IC1.21 (RB0/INT0/AN10), R7.1, SW1.3
SCLK: IC1.27 (RB6/KBI2/PGC), J7.4
SC_IN: IC1.16 (RC5/SDO); also elsewhere on the board
SDATA: IC1.28 (RB7/KBI3/PGD), J7.5
VCC: C5.1, C6.2, IC1.20 (VDD), J7.2, R1.1, R2.2, R5.2, R8.2, R31.1, R33.1, R43.2, R44.2, SW1.4, SW2.4, SW3.4, SW7.1, U2.3 (VDD), U3.16 (VDD); also elsewhere on the board
angle_m: IC1.13 (RC2/CCP1); also elsewhere on the board
reset: J4.2, R1.2, SW4.1
select_button: IC1.22 (RB1/INT1/AN8), R10.1, SW3.3

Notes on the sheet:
LDR'S ANTI-ENLLUERNAMENT
25/05/2026
BUS CAN
SW OPEN/CLOSE
USART
S'observa el microcontrolador i les seves conexions, amb la corresponent botonera per tal de poder moure els retrovisors.
MICROCONTROLADOR
BOTONERA
INPUTS
CRISTALL
Etapa Digital

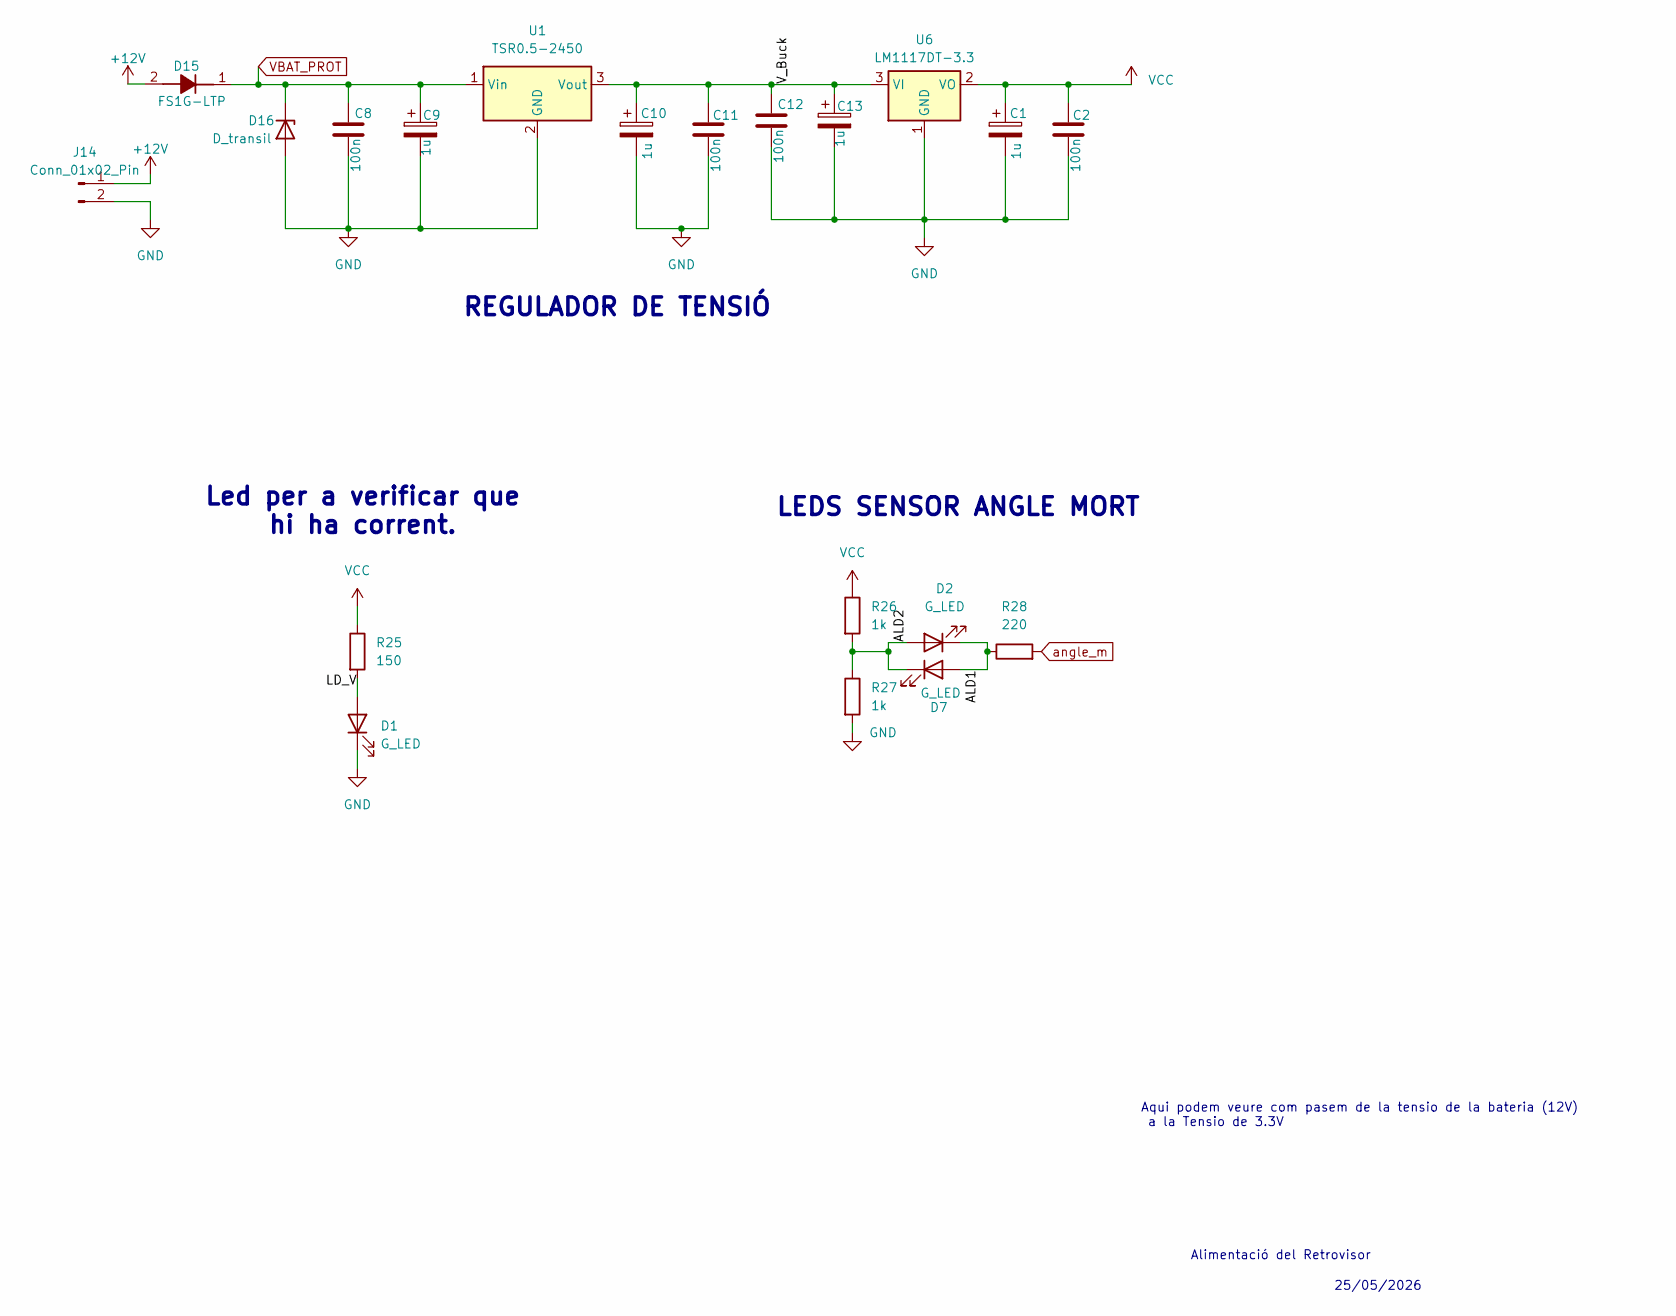
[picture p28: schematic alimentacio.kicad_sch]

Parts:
C1, C9, C10, C13: 1u; CP_Elec_4x5.7
C2, C8, C11, C12: 100n; C_0805_2012Metric_Pad1.18x1.45mm_HandSolder
D1, D2, D7: G_LED; LED_0805_2012Metric_Pad1.15x1.40mm_HandSolder
D15: FS1G-LTP; DIOM5225X244N; Manufacturer_Part_Number FS1G-LTP; Mouser Part Number 833-FS1G-LTP
D16: D_transil; D_DO-35_SOD27_P2.54mm_Vertical_AnodeUp
J14: Conn_01x02_Pin; PinHeader_1x02_P2.54mm_Vertical
R25: 150; R_0805_2012Metric_Pad1.20x1.40mm_HandSolder
R26, R27: 1k; R_1206_3216Metric_Pad1.30x1.75mm_HandSolder
R28: 220; R_1206_3216Metric_Pad1.30x1.75mm_HandSolder
U1: TSR0.5-2450; Converter_DCDC_TRACO_TSR0.5-24xx_TSR0.5-24xxx_THT
U6: LM1117DT-3.3; TO-252-3_TabPin2

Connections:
+12V: D15.2 (A), J14.1
/Alimentació/ALD1: D2.1 (K), D7.2 (A), R28.1
/Alimentació/ALD2: D2.2 (A), D7.1 (K), R26.2, R27.1
/Alimentació/LD_V: D1.2 (A), R25.2
/Alimentació/V_Buck: C10.1, C11.1, C12.1, C13.1, U1.3 (Vout), U6.3 (VI)
GND: C1.2, C2.2, C8.2, C9.2, C10.2, C11.2, C12.2, C13.2, D1.1 (K), D16.2 (A), J14.2, R27.2, U1.2 (GND), U6.1 (GND); also elsewhere on the board
VBAT_PROT: C8.1, C9.1, D15.1 (K), D16.1 (K), U1.1 (Vin); also elsewhere on the board
VCC: C1.1, C2.1, R25.1, R26.1, U6.2 (VO); also elsewhere on the board
angle_m: R28.2; also elsewhere on the board

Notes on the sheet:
REGULADOR DE TENSIÓ
25/05/2026
Led per a verificar que hi ha corrent.
LEDS SENSOR ANGLE MORT
Aqui podem veure com pasem de la tensio de la bateria (12V) a la Tensio de 3.3V
Alimentació del Retrovisor

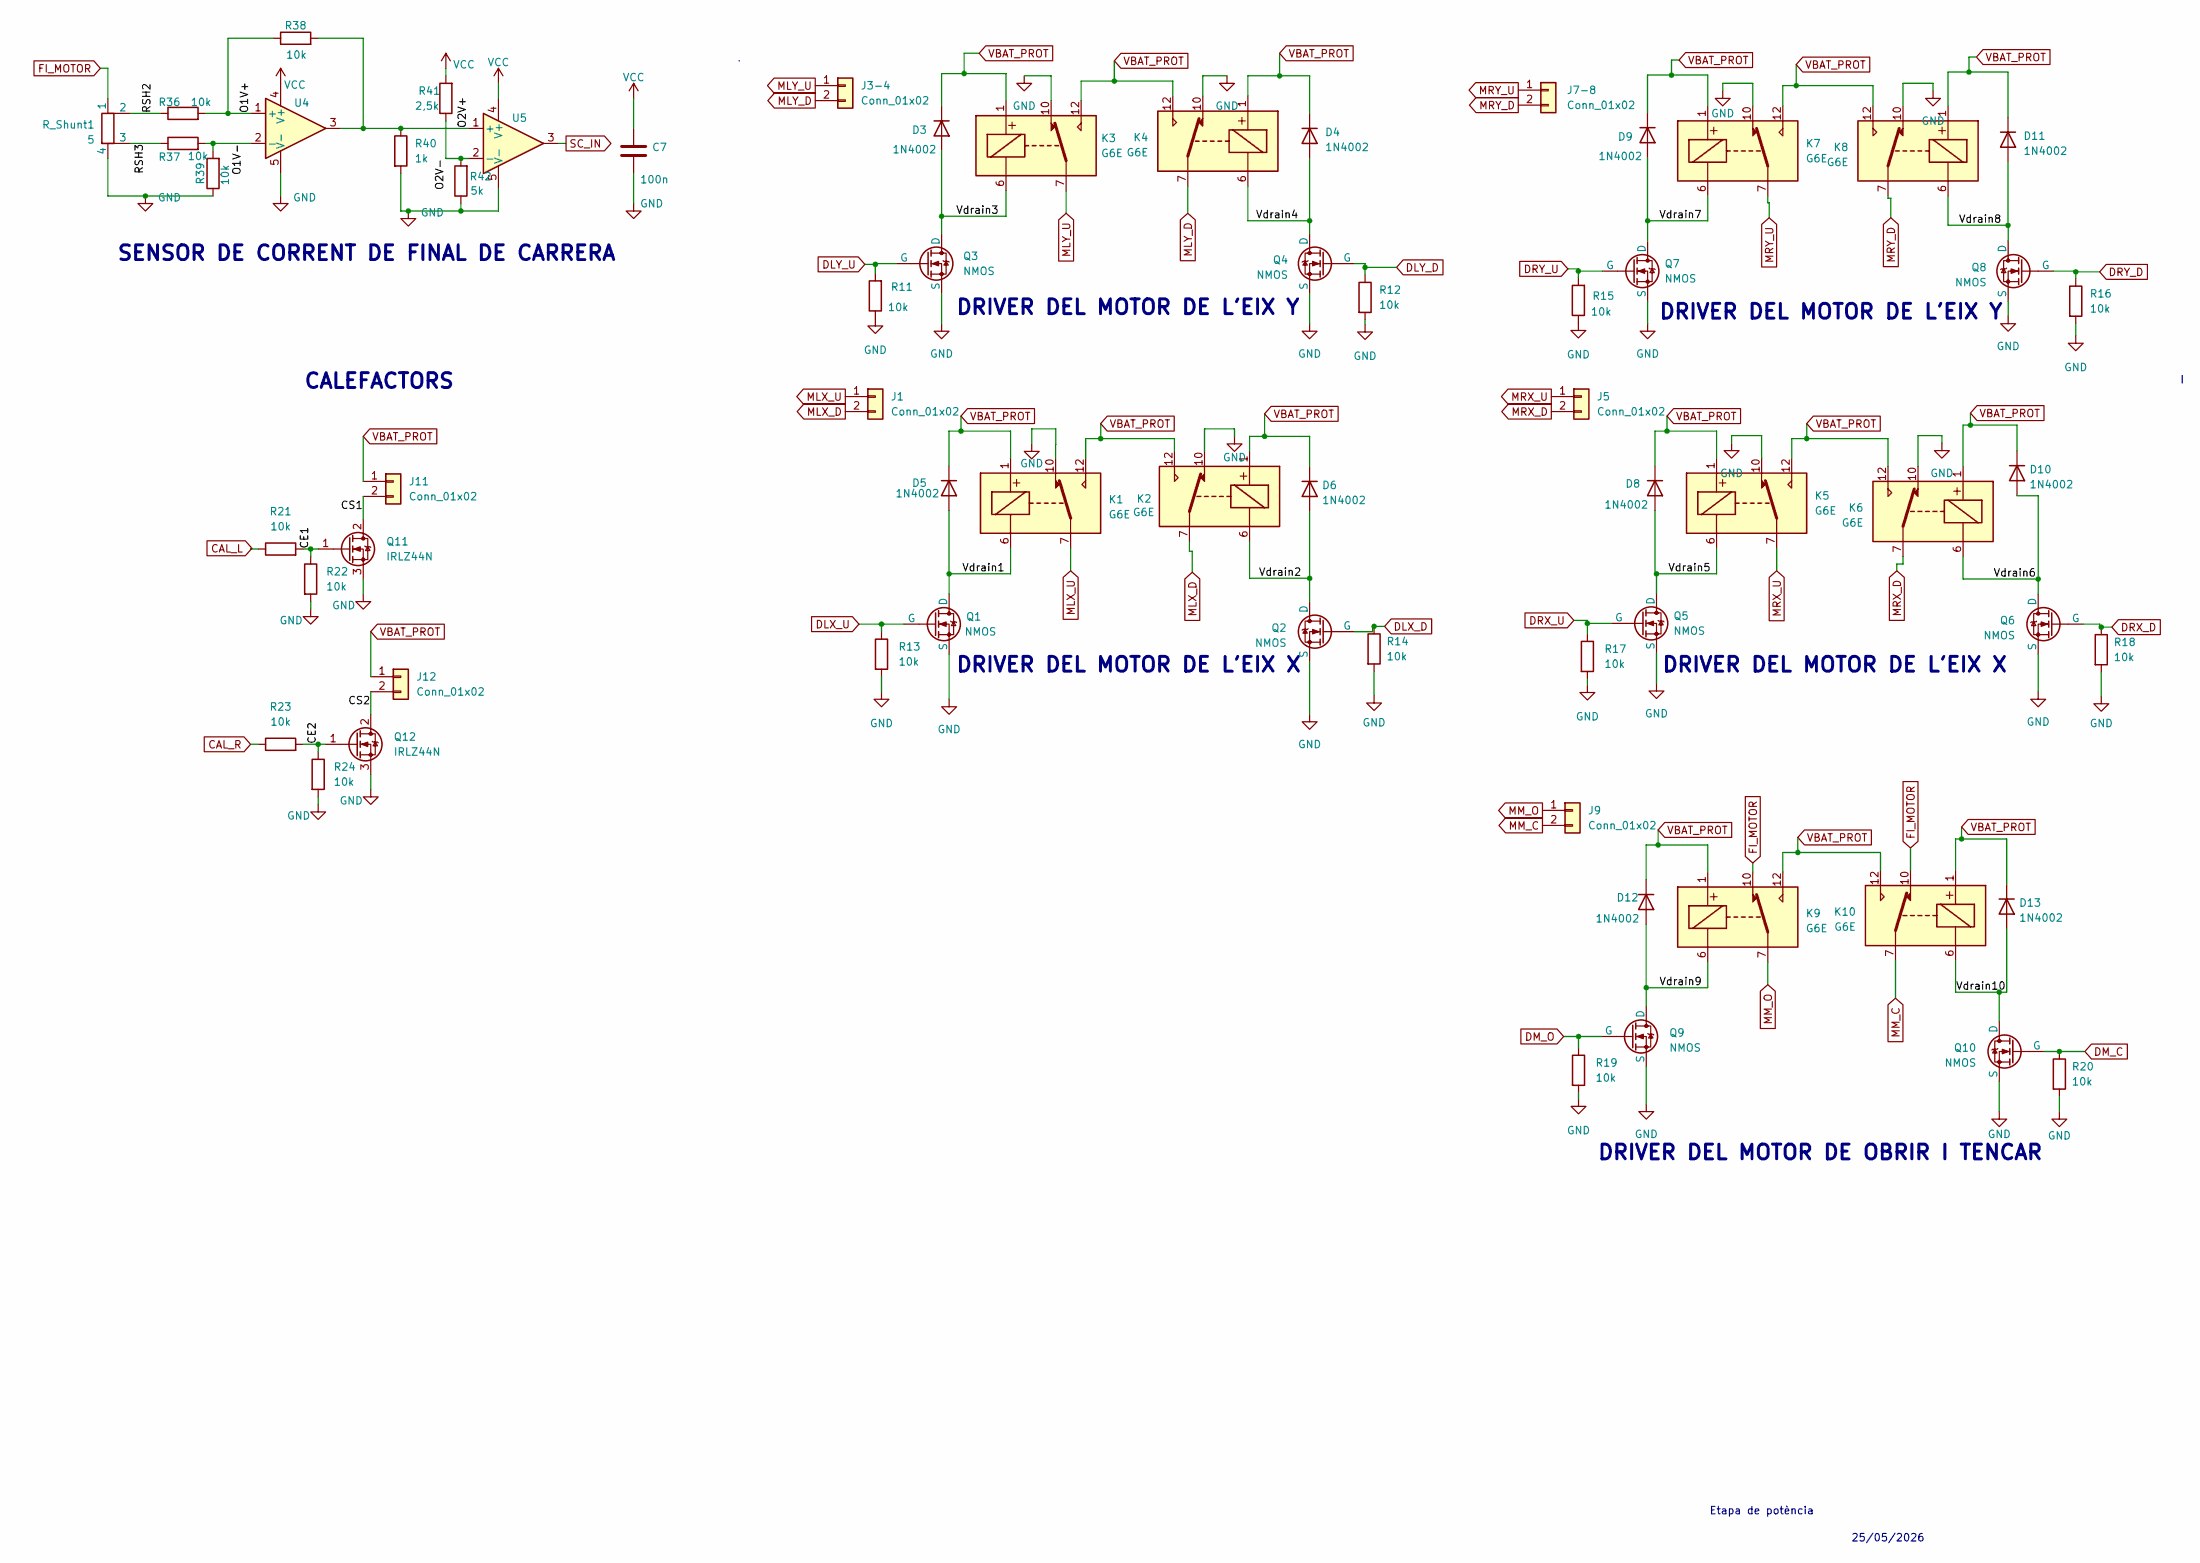
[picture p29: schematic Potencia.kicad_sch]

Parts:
C7: 100n; C_0805_2012Metric_Pad1.18x1.45mm_HandSolder
D3, D4, D5, D6, D8, D9, D10, D11, D12, D13: 1N4002; D_DO-41_SOD81_P10.16mm_Horizontal
J1, J3-4, J5, J7-8, J9, J11, J12: Conn_01x02; PinHeader_1x02_P2.54mm_Vertical
K1, K2, K3, K4, K5, K6, K7, K8, K9, K10: G6E; Relay_SPDT_Omron_G6E
Q1, Q2, Q3, Q4, Q5, Q6, Q7, Q8, Q9, Q10: NMOS; TO254P470X1016X1965-3P
Q11, Q12: IRLZ44N; TO-220-3_Vertical
R11, R12, R13, R14, R15, R16, R17, R18, R19, R20, R21, R22, R23, R24, R36, R37, R38, R39: 10k; R_1206_3216Metric_Pad1.30x1.75mm_HandSolder
R40: 1k; R_1206_3216Metric_Pad1.30x1.75mm_HandSolder
R41: 2,5k; R_1206_3216Metric_Pad1.30x1.75mm_HandSolder
R42: 5k; R_1206_3216Metric_Pad1.30x1.75mm_HandSolder
R_Shunt1: 5; R_Shunt_Ohmite_LVK12
U4, U5: type="X" model="OPAMP" lib=""; SOT95P280X145-5N

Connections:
/Potencia/CE1: Q11.1 (G), R21.2, R22.1
/Potencia/CE2: Q12.1 (G), R23.2, R24.1
/Potencia/CS1: J11.2, Q11.2 (D)
/Potencia/CS2: J12.2, Q12.2 (D)
/Potencia/O1V+: R36.2, R38.1, U4.1 (+)
/Potencia/O1V-: R37.2, R39.2, U4.2 (-)
/Potencia/O2V+: R38.2, R40.1, U4.3, U5.1 (+)
/Potencia/O2V-: R41.1, R42.2, U5.2 (-)
/Potencia/RSH2: R36.1, R_Shunt1.2
/Potencia/RSH3: R37.1, R_Shunt1.3
/Potencia/Vdrain1: D5.2 (A), K1.6, Q1.1 (D)
/Potencia/Vdrain2: D6.2 (A), K2.6, Q2.1 (D)
/Potencia/Vdrain3: D3.2 (A), K3.6, Q3.1 (D)
/Potencia/Vdrain4: D4.2 (A), K4.6, Q4.1 (D)
/Potencia/Vdrain5: D8.2 (A), K5.6, Q5.1 (D)
/Potencia/Vdrain6: D10.2 (A), K6.6, Q6.1 (D)
/Potencia/Vdrain7: D9.2 (A), K7.6, Q7.1 (D)
/Potencia/Vdrain8: D11.2 (A), K8.6, Q8.1 (D)
/Potencia/Vdrain9: D12.2 (A), K9.6, Q9.1 (D)
/Potencia/Vdrain10: D13.2 (A), K10.6, Q10.1 (D)
CAL_L: R21.1; also elsewhere on the board
CAL_R: R23.1; also elsewhere on the board
DLX_D: Q2.2 (G), R14.1; also elsewhere on the board
DLX_U: Q1.2 (G), R13.1; also elsewhere on the board
DLY_D: Q4.2 (G), R12.1; also elsewhere on the board
DLY_U: Q3.2 (G), R11.2; also elsewhere on the board
DM_C: Q10.2 (G), R20.1; also elsewhere on the board
DM_O: Q9.2 (G), R19.1; also elsewhere on the board
DRX_D: Q6.2 (G), R18.1; also elsewhere on the board
DRX_U: Q5.2 (G), R17.1; also elsewhere on the board
DRY_D: Q8.2 (G), R16.1; also elsewhere on the board
DRY_U: Q7.2 (G), R15.2; also elsewhere on the board
FI_MOTOR: K9.10, K10.10, R_Shunt1.1
GND: C7.2, K1.10, K2.10, K3.10, K4.10, K5.10, K6.10, K7.10, K8.10, Q1.3 (S), Q2.3 (S), Q3.3 (S), Q4.3 (S), Q5.3 (S), Q6.3 (S), Q7.3 (S), Q8.3 (S), Q9.3 (S), Q10.3 (S), Q11.3 (S), Q12.3 (S), R11.1, R12.2, R13.2, R14.2, R15.1, R16.2, R17.2, R18.2, R19.2, R20.2, R22.2, R24.2, R39.1, R40.2, R42.1, R_Shunt1.4, U4.5 (V-), U5.5 (V-); also elsewhere on the board
MLX_D: J1.2, K2.7
MLX_U: J1.1, K1.7
MLY_D: J3-4.2, K4.7
MLY_U: J3-4.1, K3.7
MM_C: J9.2, K10.7
MM_O: J9.1, K9.7
MRX_D: J5.2, K6.7
MRX_U: J5.1, K5.7
MRY_D: J7-8.2, K8.7
MRY_U: J7-8.1, K7.7
SC_IN: U5.3; also elsewhere on the board
VBAT_PROT: D3.1 (K), D4.1 (K), D5.1 (K), D6.1 (K), D8.1 (K), D9.1 (K), D10.1 (K), D11.1 (K), D12.1 (K), D13.1 (K), J11.1, J12.1, K1.1, K1.12, K2.1, K2.12, K3.1, K3.12, K4.1, K4.12, K5.1, K5.12, K6.1, K6.12, K7.1, K7.12, K8.1, K8.12, K9.1, K9.12, K10.1, K10.12; also elsewhere on the board
VCC: C7.1, R41.2, U4.4 (V+), U5.4 (V+); also elsewhere on the board

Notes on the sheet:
25/05/2026
DRIVER DEL MOTOR DE OBRIR I TENCAR
SENSOR DE CORRENT DE FINAL DE CARRERA
Etapa de potència
DRIVER DEL MOTOR DE L'EIX Y
DRIVER DEL MOTOR DE L'EIX X
CALEFACTORS

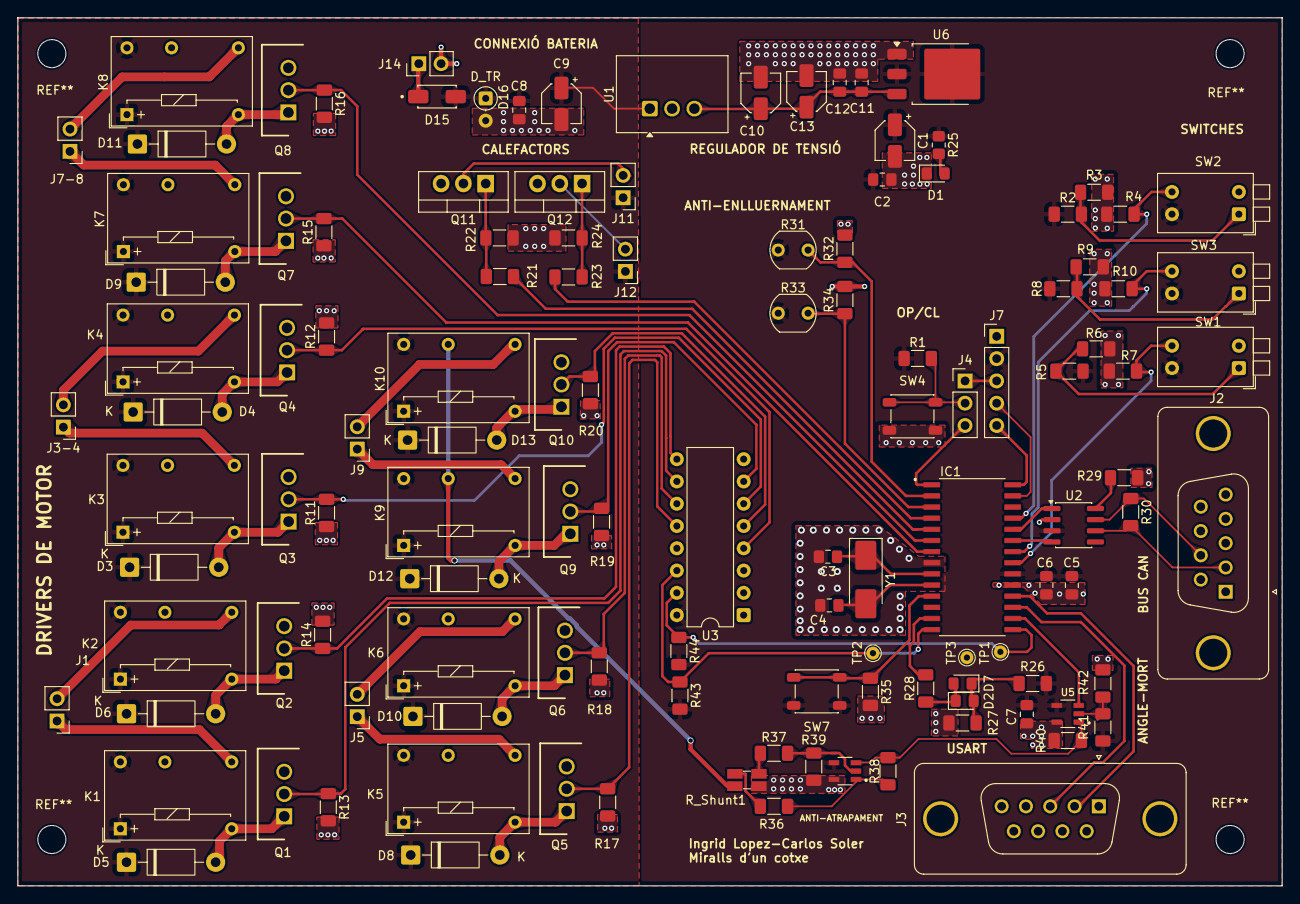
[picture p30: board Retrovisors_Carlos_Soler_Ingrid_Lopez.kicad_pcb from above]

Board: 2 copper layers, 144.1 x 99.0 mm, 123 parts (0 on the bottom side), 78 nets.

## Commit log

2026-03-17 Create project kicad
    [Retrovisors_Carlos_Soler_Ingrid_Lopez.kicad_pcb, Retrovisors_Carlos_Soler_Ingrid_Lopez.kicad_sch]
2026-03-17 Inici kiCat
    [Retrovisors_Carlos_Soler_Ingrid_Lopez.kicad_sch]
2026-03-17 Etapa de alimentació 1
    [Retrovisors_Carlos_Soler_Ingrid_Lopez.kicad_sch]
2026-03-17 Etapa de alimentacio completa
    [Retrovisors_Carlos_Soler_Ingrid_Lopez.kicad_sch]
2026-03-17 Alimentacio finalitzada e inici de micro
    [Retrovisors_Carlos_Soler_Ingrid_Lopez.kicad_sch]
2026-03-18 microcontrolador i driver
    [Retrovisors_Carlos_Soler_Ingrid_Lopez.kicad_sch]
2026-03-22 Correcio gnd, proposicio canvi de micro
    [Retrovisors_Carlos_Soler_Ingrid_Lopez.kicad_sch]
2026-03-23 Reorganització proyecte, inici conexions CAN
    [Alimentació.kicad_sch, Potencia.kicad_sch, Retrovisors_Carlos_Soler_Ingrid_Lopez.kicad_sch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]
2026-03-23 Part Micro quasi completat, falta afegir etiquetes de potencia
    [Potencia.kicad_sch, untitled.kicad_sch]
2026-03-24 Microprocessador finalissim + placement de alimentacion y micro
    [Alimentació.kicad_sch, Digital.kicad_sch, Potencia.kicad_sch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]
2026-03-25 Diagrama de Blocs Afegit, mes canvi del swicht1 to push botton5
    [Digital.kicad_sch]
2026-03-29 Creacio de branca nova i update
    [Alimentació.kicad_sch, Digital.kicad_sch, Potencia.kicad_sch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]
2026-04-07 actualització (NO VERSIÓ FINAL)
    [Retrovisors_Carlos_Soler_Ingrid_Lopez.kicad_sch]
2026-04-08 esquematic + placement (FALTA ROUTING DELS DRIVERS!!)
    [Retrovisors_Carlos_Soler_Ingrid_Lopez.kicad_pcb, Retrovisors_Carlos_Soler_Ingrid_Lopez.kicad_sch]
2026-04-08 añadido el readme
    [Retrovisors_Carlos_Soler_Ingrid_Lopez.kicad_sch]
2026-04-08 Modificació placement
    [Retrovisors_Carlos_Soler_Ingrid_Lopez.kicad_pcb, Retrovisors_Carlos_Soler_Ingrid_Lopez.kicad_sch]
2026-04-08 prueba para unir a la main
    [Retrovisors_Carlos_Soler_Ingrid_Lopez.kicad_pcb]
2026-04-08 modificando todos los GND eliminamos GND PWR
    [Digital.kicad_sch, Potencia.kicad_sch, Retrovisors_Carlos_Soler_Ingrid_Lopez.kicad_pcb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]
2026-04-10 millora de placement
    [Retrovisors_Carlos_Soler_Ingrid_Lopez.kicad_pcb]
2026-04-13 Enrotament Part digital finalitzada
    [Potencia.kicad_sch, Retrovisors_Carlos_Soler_Ingrid_Lopez.kicad_pcb]
2026-04-14 canvis en el readme, a més de petites modificacions de PCB part digital
    [Digital.kicad_sch, Retrovisors_Carlos_Soler_Ingrid_Lopez.kicad_pcb]
2026-04-14 correccio error historial de canvis
2026-04-14 afegir expansor de i2C de 8 pins
    [Retrovisors_Carlos_Soler_Ingrid_Lopez.kicad_pcb]
2026-04-14 afegit esquematic (testpoints + extensor de pines) falta acabar placement
    [Digital.kicad_sch, Potencia.kicad_sch]
2026-04-14 canvis placement, afegir els r4emplazos que hi han a la pcb
    [Digital.kicad_sch, Retrovisors_Carlos_Soler_Ingrid_Lopez.kicad_pcb]
2026-04-15 correcions de pcb
    [Digital.kicad_sch, Retrovisors_Carlos_Soler_Ingrid_Lopez.kicad_pcb, Retrovisors_Carlos_Soler_Ingrid_Lopez.kicad_sch]
2026-04-18 placa abans de canvi placement 1
    [Retrovisors_Carlos_Soler_Ingrid_Lopez.kicad_pcb]
2026-04-18 pcb Tota connectada
    [Digital.kicad_sch, Retrovisors_Carlos_Soler_Ingrid_Lopez.kicad_pcb]
2026-04-20 final de pcb, falta els test points
    [Digital.kicad_sch, Potencia.kicad_sch, Retrovisors_Carlos_Soler_Ingrid_Lopez.kicad_pcb]
2026-04-21 petites modificacions resistencies part digital + resolucio errors pcb
    [Digital.kicad_sch, Potencia.kicad_sch, Retrovisors_Carlos_Soler_Ingrid_Lopez.kicad_pcb]
2026-04-27 canvis pcb finals
    [Digital.kicad_sch, Potencia.kicad_sch, Retrovisors_Carlos_Soler_Ingrid_Lopez.kicad_pcb]
2026-04-27 pcb definitiva
    [Digital.kicad_sch, Potencia.kicad_sch, Retrovisors_Carlos_Soler_Ingrid_Lopez.kicad_pcb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]
2026-04-28 placa definitivisima
    [Retrovisors_Carlos_Soler_Ingrid_Lopez.kicad_pcb]
2026-04-28 diseny final final
    [Digital.kicad_sch, Potencia.kicad_sch, Retrovisors_Carlos_Soler_Ingrid_Lopez.kicad_pcb]
2026-04-29 afegit tot final
    [Digital.kicad_sch, Potencia.kicad_sch, Retrovisors_Carlos_Soler_Ingrid_Lopez.csv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]
2026-04-29 Version final + readme
    [pressupost.xlsx]
